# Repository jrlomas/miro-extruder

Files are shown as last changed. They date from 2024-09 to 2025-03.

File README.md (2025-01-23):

# Miró Extruder (Public **Beta**)
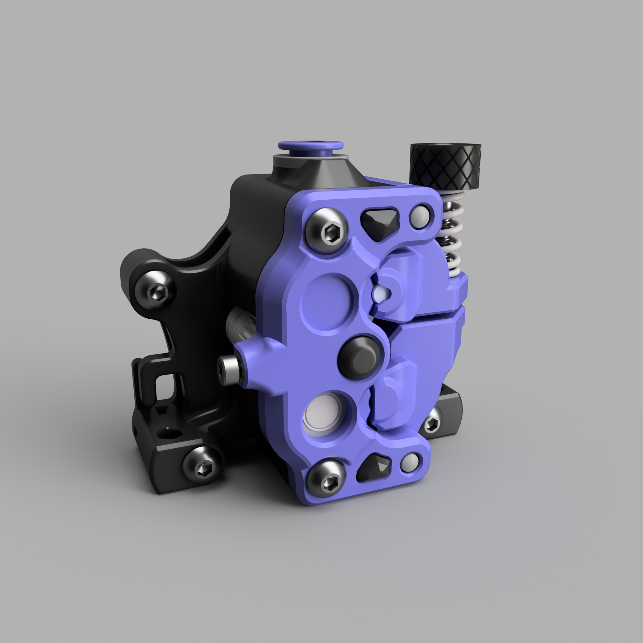
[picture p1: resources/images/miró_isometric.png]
Miró Extruder


## General Information

The **Miró Extruder** is a high-performance, dual-drive 3D printer extruder, engineered to provide precise and reliable filament control using two sets of dual-drive gears. It features a compact design and is fully compatible with the Sherpa Mini extruder's bolt pattern.

Unlike my previous **Sherpa Mini Crew** design, the Miró is a completely new creation with no work derived from **Annex Engineering**. While it was inspired by the Sherpa Mini, the Miró is an entirely independent design, not a derivative of the Sherpa Mini extruder.

This extruder is the result of a collaboration between  **knight_rad.iant** and **wick69** in Discord, with notable testers such as **Meelis** (Discord).

For any questions, feedback, or suggestions, please use the GitHub Issues page. We appreciate your support and hope the **Miró Extruder** enhances your 3D printing experience!

> **Note:** Only STL files are provided in this repository.

---

## Bill of Materials (BOM)

| Part Name | Quantity | Notes |
|---|---|---|
| 5mm OD x 8mm Length Shaft | 1 | |
| 5mm OD x 18mm Length Shaft | 1 | |
| MR85ZZ Bearing | 3 | |
| Bondtech EXT-KIT-100 | 1 | |
| Bondtech EXT-KIT33 | 1 | |
| ECAS04 Collet | 1 | |
| 3mm OD x 28mm Length Shaft | 2 | |
| M3 Nut | 1 | |
| NEMA 14 Pancake Stepper Motor | 1 | |
| M2 Heat Set Insert | 1 | [3.6mm OD x 4mm length](https://www.amazon.com/gp/product/B08T7NDPQC)|
| M2 x 6mm Screw | 1 | Use Loctite to ensure alignment |
| M2 x 8mm Screw | 1 | Optionally if using the built-in filament runout sensor |
| Small gauge wire (26AWG or 28AWG) (black and red) | enough to reach toolhead board | Optionally if using the built-in filament runout sensor |

---

## Printing Instructions

Print **one of each** of the following parts:

- [`miró_body_x1.stl`](STLs/miró_body_x1.stl)
- [`miró_rear_x1.stl`](STLs/miró_rear_x1.stl)
- [`miró_upper_guilder[a]_x1.stl`](STLs/miró_upper_guilder[a]_x1.stl)
- [`miró_lower_guilder[a]_x1.stl`](STLs/miró_lower_guilder[a]_x1.stl)

For the front cover, choose **one** of the following options:

- [`miró_front[a].stl`](STLs/miró_front[a].stl) standard front cover
- [`miró_front_k[a].stl`](STLs/miró_front_k[a].stl) extended cover with a third attachment point

Optionally, you can print [`miró_thumbscrew.stl`](STLs/miró_thumbscrew.stl) if you prefer a printed thumbscrew over a standard M3 thumbscrew. You will also need an M3 x 25mm screw, which should be inserted into the printed part using a soldering iron with an appropriate tip.

### Recommended Print Settings
- Material: ABS
- Nozzle Size: 0.4mm
- Layer Height: 0.2mm
- Perimeters: 4
- Top/Bottom Layers: 5
- Infill: 40% or higher

## Orientation

Only the **guider** parts require supports (touching build plate only). Ensure that the parts are oriented for printing as shown in the provided STLs.

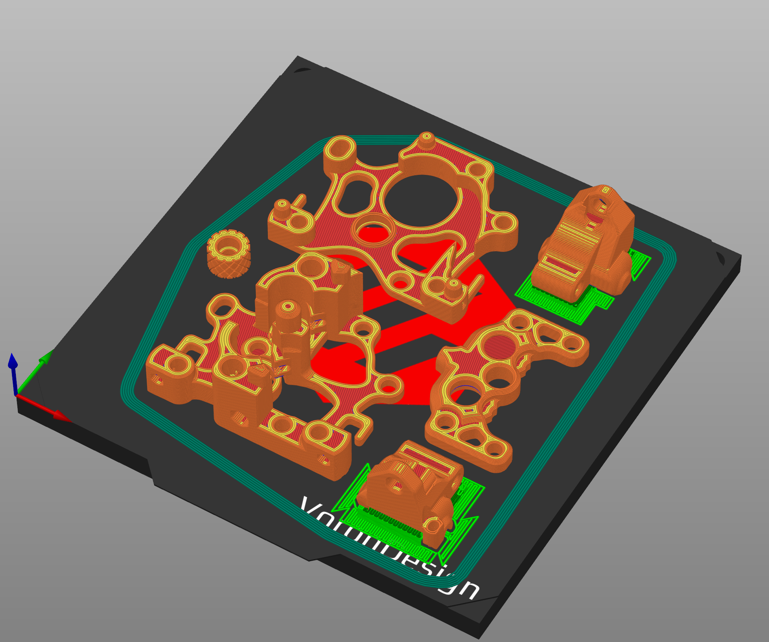
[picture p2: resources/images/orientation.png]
orientation


### Important Note about Extrusion Multiplier (EM)

It’s essential to calibrate the extrusion multiplier (EM) on your printer. These parts are designed to fit tightly, and incorrect EM settings will result in improper alignment. If the main body or rear body feels too tight, reduce your EM until the parts fit comfortably.

---

## Assembly Instructions

No written assembly instructions are provided, but a video guide is available:  
[Assembly Video](resources/videos/miró_assembly.mp4)

Check it out also on [YouTube](https://www.youtube.com/watch?v=lkKy52AsoPM)

---

## Important Assembly Notes

- The right M3 button head screw the main body, rear body, and NEMA 14 motor mount is difficult to access when the extruder is fully assembled. It is recommended to install this screw before assembling the guilders and the front cover.  The video guide demonstrates this process.
- The **upper drive gear** should be installed **without** the set screw.
- The **5mm x 20mm shaft** should be lubricated with EP2 grease.

When assembly is complete, use **Loctite** on the **M2 x 6mm screw** that pushes the **3mm shaft** for the middle idler. This screw is crucial for maintaining proper gear meshing, and the extruder will not function correctly without it.

### Alignment Procedure:
1. Completely loosen the tensioner.
2. Apply Loctite to the M2 x 6mm screw.
3. Tighten the screw until you feel medium resistance.
4. Manually rotate the **POM 50T gear** and check for any binding.
5. If binding occurs, loosen the screw in 1/8 turn increments, repeating the process until the binding is resolved.

Alternatively, you can tighten the tenionser screw until it very lightly starts to bind, and then back off the screw 1/8 of a turn, this should set the correct distance, as the this the M2 screw has a pitch of 0.4mm per turn, hence a 45° turn gives a linear distance 0.05mm

If you find the the screw bottoming and the gears are not binding, that means your gear set combination has the magic design alignment distance of 8.6mm between the gears.  You can then leave the screw fully tightened and you are done.

## Built-in Filament Sensor

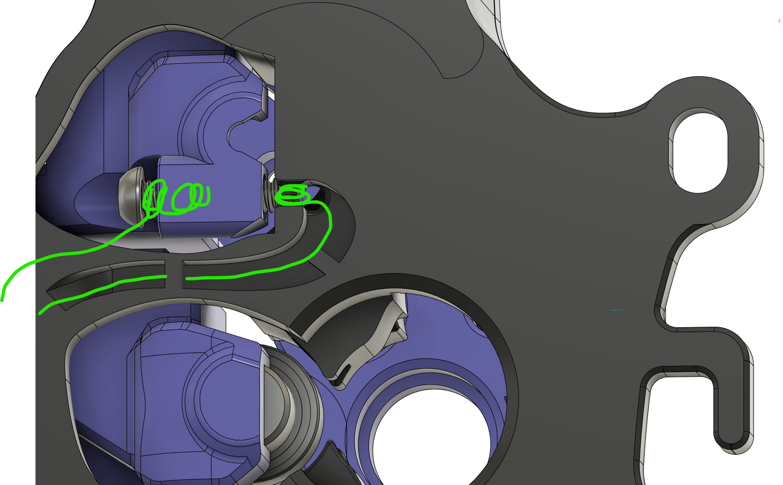
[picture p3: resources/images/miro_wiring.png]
Sensor Wiring


The Miró Extruder includes a built-in filament runout sensor of the "unklicky" type. The sensor is created using just two pieces of wire and an M2 screw. The upper guide arm has an M2 hole that fits an M2 x 8mm screw. To set it up, wrap a small-gauge wire around the screw and insert it into the hole, positioning it at the right distance to make contact with another set of wires wrapped around the main body of the extruder.

The unklicky sensor is normally closed when no filament is present. Once the filament is inserted, the upper guide expands, breaking the contact. You can adjust the M2 screw to fine-tune the contact distance. Additionally, thanks to the extruder’s dual set of gears, it's possible to detect filament runout and still retract the remaining filament easily, ensuring smooth operation even during filament changes.

The other ends of the wires can be crimped to a JST connector and plugged into your printer’s filament sensor input. One wire should be connected to GND, and the other to a port configured with an internal pull-up resistor. In Klipper firmware, you can do this by adding a `^` before the pin number in the `filament_sensor` section of the `printer.cfg` file.

Here's an example configuration for a sensor connected to the PC2 pin:

```yaml
[filament_switch_sensor RunoutSensor]
pause_on_runout: False
runout_gcode: PAUSE
insert_gcode: RESUME
switch_pin: ^!PC2
```

This is a picture of rear with the filament sensor assembled:
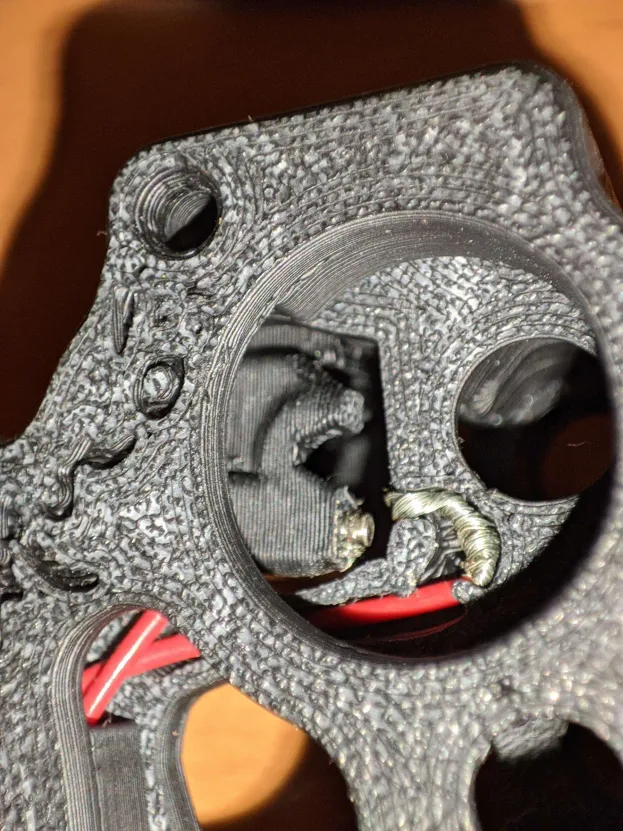
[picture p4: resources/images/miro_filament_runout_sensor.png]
Sensor Assembly

## Distances and Measurements
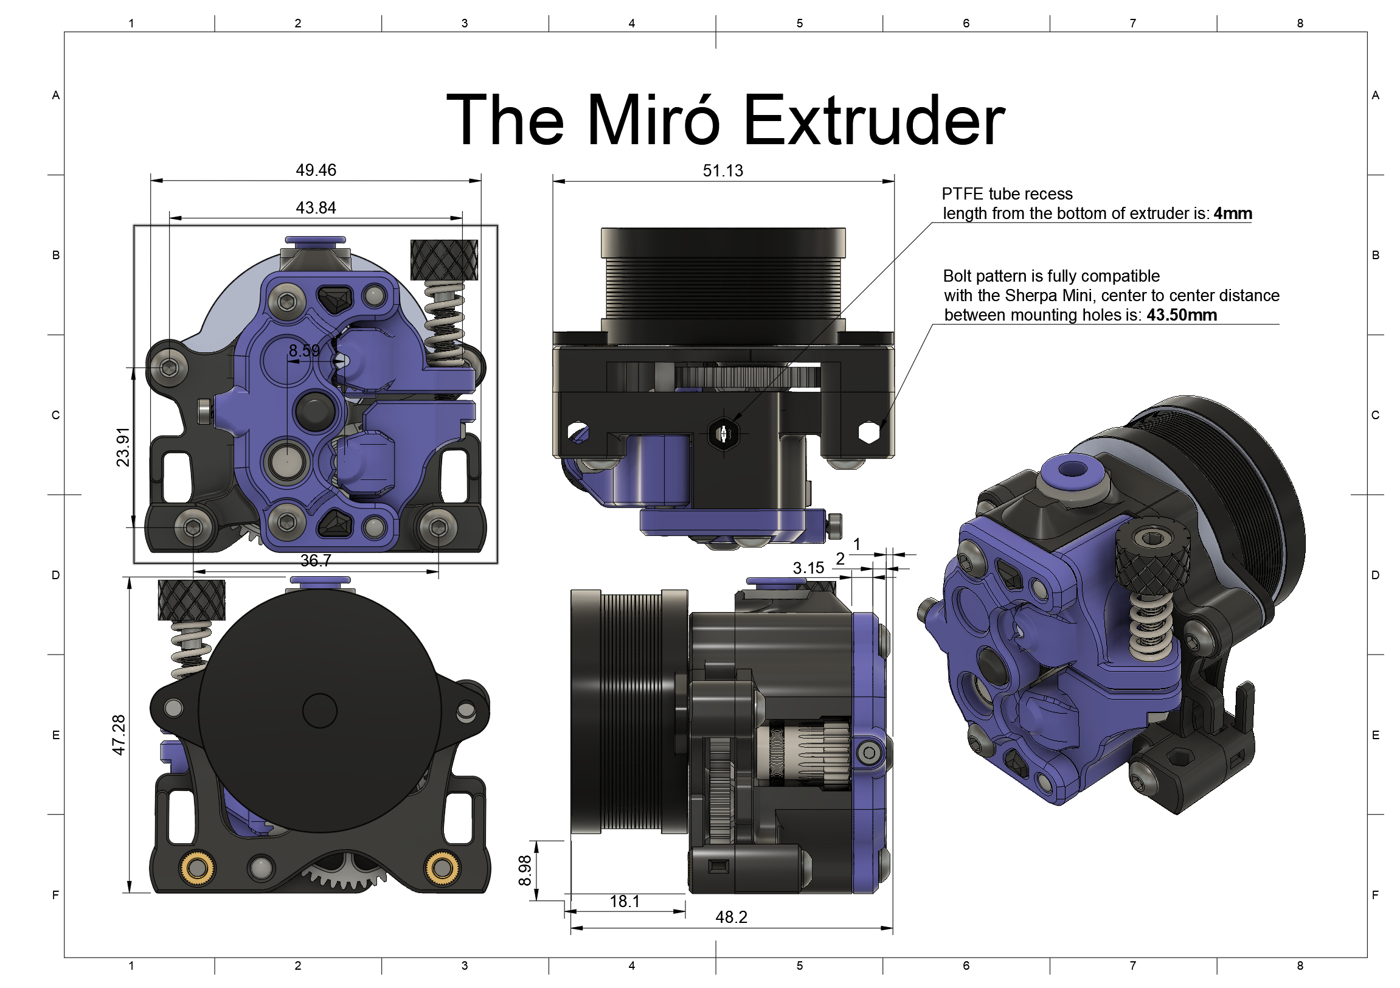
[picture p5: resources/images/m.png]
Distances


---

## License

This project is licensed under the [Creative Commons - Attribution - Non-Commercial - No Derivatives](LICENSE-CC-BY-NC-ND-4.0.md) license.

For commercial use inquiries, please contact **knight_rad.iant** or **wick69** on Discord.

---

## Credits

This project is a collaboration between **wick69** and **knight_rad.iant** on Discord.

© 2023-2024 by the authors. All rights reserved.

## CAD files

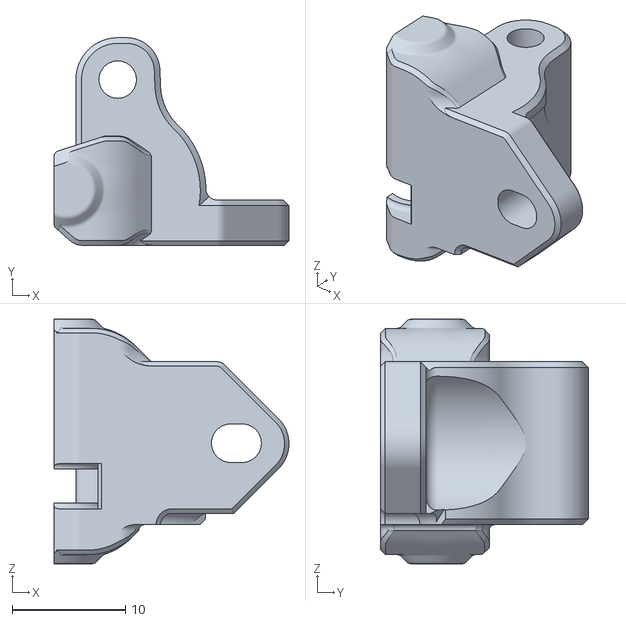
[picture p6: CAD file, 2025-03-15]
STLs/miró_upper_guilder_smooth_bearing_opt[a].stl
20.8 x 18.3 x 21.6

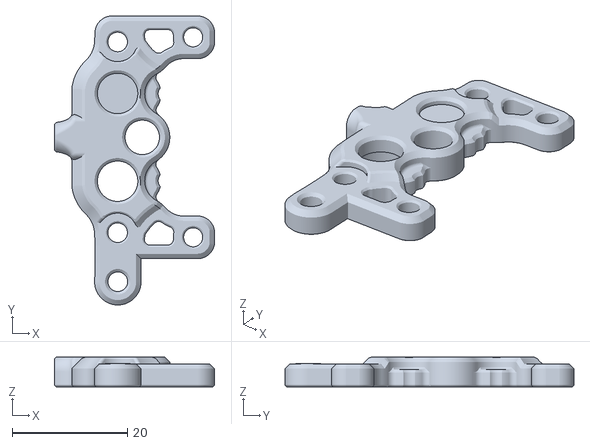
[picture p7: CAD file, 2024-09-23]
STLs/miró_front_k[a].stl
27.7 x 50.1 x 5.15

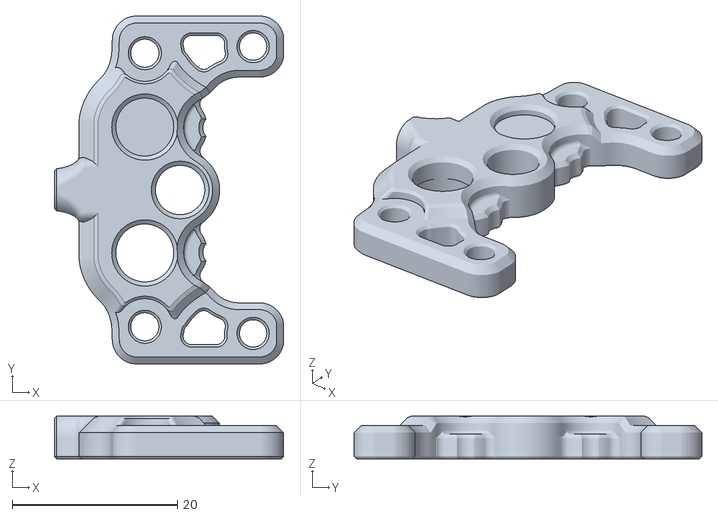
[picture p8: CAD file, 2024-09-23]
STLs/miró_front[a].stl
27.7 x 42.1 x 5.15

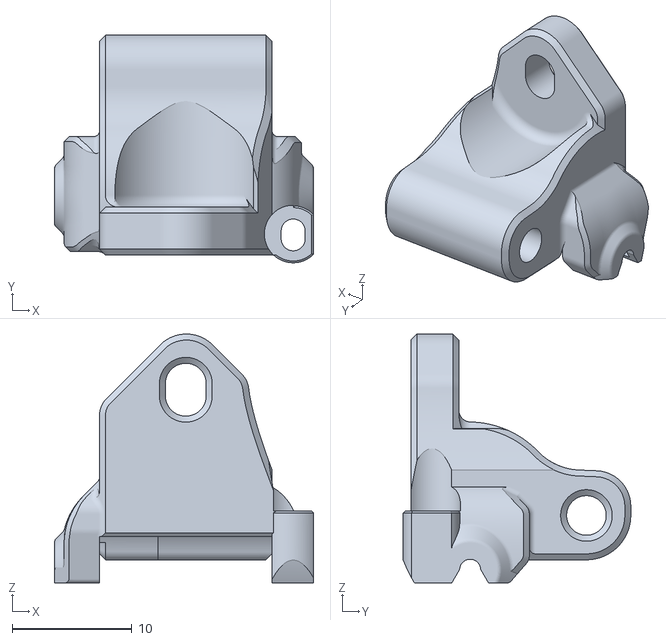
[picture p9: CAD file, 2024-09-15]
STLs/miró_upper_guilder[a]_x1.stl
21.6 x 19.0 x 20.8

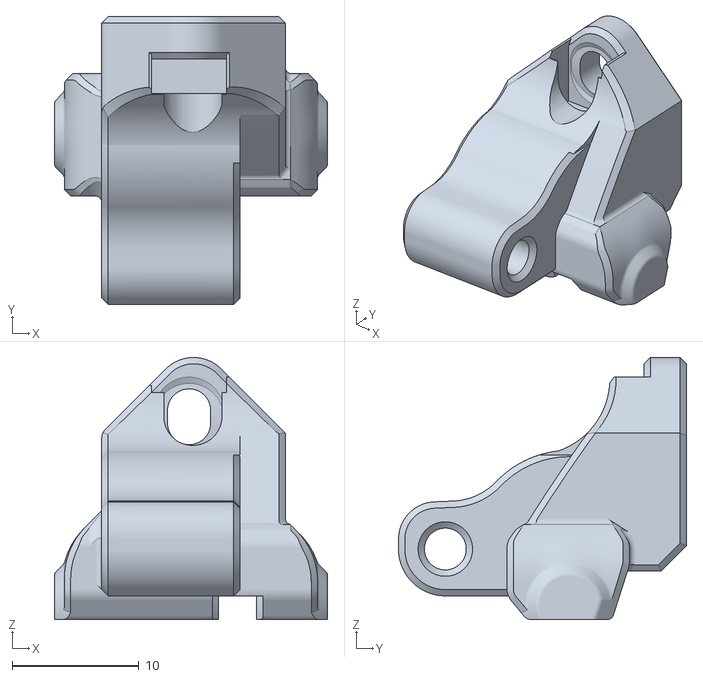
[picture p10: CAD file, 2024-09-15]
STLs/miró_lower_guilder[a]_x1.stl
21.6 x 22.7 x 20.7

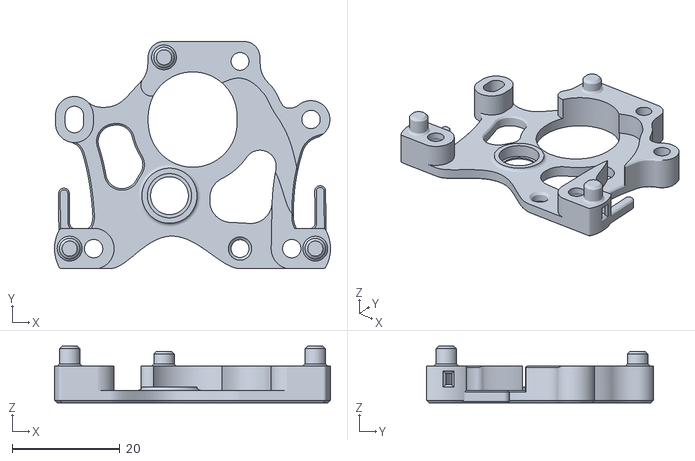
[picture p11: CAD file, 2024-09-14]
STLs/miró_rear_x1.stl
51.1 x 42.1 x 10.6

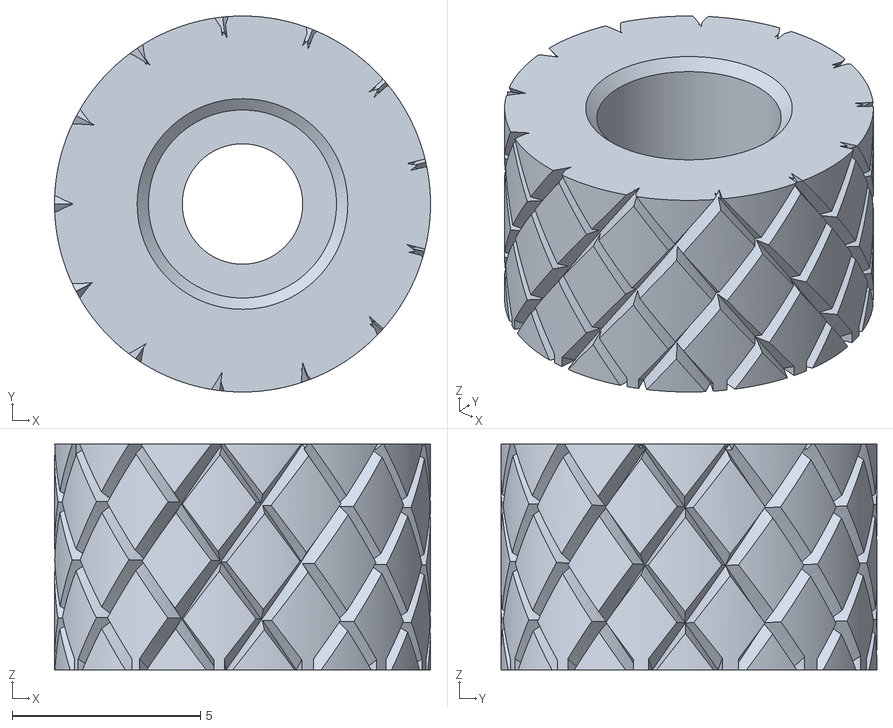
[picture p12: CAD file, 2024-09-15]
STLs/miró_thumbscrew.stl
10.00 x 10.00 x 6.00

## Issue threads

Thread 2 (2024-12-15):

Any chance someone can confirm this extruder works drop in for a dragon burner?

marcell-janovszki, 2024-12-15:
Looking to use this for a dragon burner, has anyone else tried this yet?
Just drop in with the dragon burner body?

shoeys-for-newey, 2024-12-22:
I haven't used dragon burner but if it's compatible with Sherpa Mini, the Miro will also work

shoeys-for-newey, 2024-12-22:
> Looking to use this for a dragon burner, has anyone else tried this yet? Just drop in with the dragon burner body?

If it's compatible with Sherpa Mini, it will be drop-in compatible with Miro

Closed 2025-01-17.

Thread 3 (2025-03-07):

Why no derivatives license?

Ataraxia-Mechanica, 2025-03-07:
I have an extra guider gear laying around so I can buy only one extra set of gears, use two bearings and modify the extruder to fit. But since it's no derivatives nobody else could use the design. Oh well.

Closed 2025-03-15.

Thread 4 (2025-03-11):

Optional smooth bearing upper guilder is offset

Ataraxia-Mechanica, 2025-03-11:
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

jrlomas, 2025-03-15:
This issue is now solved https://github.com/jrlomas/miro-extruder/commit/b9e8885d941322ca915e9c603aaa5a409f99d671

Closed 2025-03-15.

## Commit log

2024-09-14 Initial release
    [miró_front[a].stl, miró_front_k[a].stl, miró_lower_guider[a]_x1.stl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]
2024-09-15 Addition of smooth bearing upper guilder
    [miró_upper_guilder_smooth_bearing_opt[a].stl]
2024-09-15 Correctly oriented the guilders and thumbscrew STLs
    [miró_lower_guider[a]_x1.stl, miró_lower_guilder[a]_x1.stl, miró_thumbscrew.stl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]
2024-09-15 Updated nozzle size on README.md
2024-09-23 Correction to distances for 20mm upper pins
    [miró_front[a].stl, miró_front_k[a].stl]
2024-09-23 Added note about right M3 and correct sequence during assembly
2024-09-23 Added instructions for filament runout switch
2024-09-23 Added size of M2 insert
2025-01-23 Update README.md
    Shaft length should be 18mm not 20mm
2025-03-15 Correction to align optional upper guilder with filament path.
    [miró_upper_guilder_smooth_bearing_opt[a].stl]
